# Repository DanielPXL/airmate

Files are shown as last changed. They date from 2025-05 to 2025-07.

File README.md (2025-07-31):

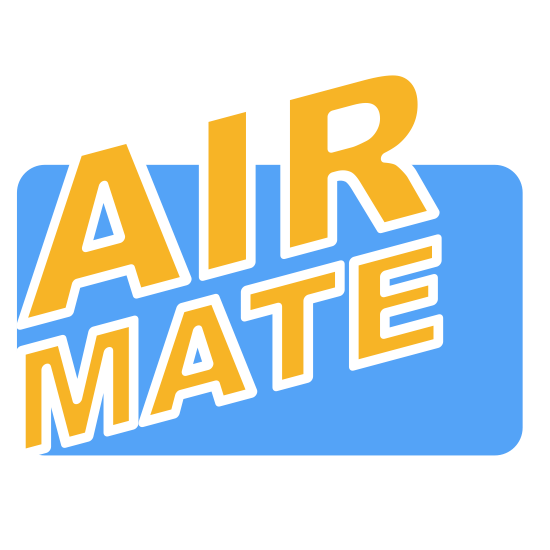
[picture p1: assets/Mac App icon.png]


---

Der _AirMate_ ist ein sich automatisch öffnendes Fenster, welches sich anhand von Sensordaten selbst öffnet. Er hostet außerdem eine Website, welche die Sensordaten anzeigt. Über diese und einen Knopf am Fenster selbst lässt sich das Fenster auch manuell öffnen.

Als Projekt ist es im Rahmen eines Moduls des Informatikstudiums entstanden. Es hatte dabei die Zielsetzung eines der Nachhaltigkeitsziele der UN zu erfüllen. Wir haben uns hier auf das Ziel der Inklusion konzentriert und haben ein Konzept erstellt welches Menschen mit Einschränkungen das alltägliche Leben leichter machen soll. Da wir mit dem CO2- und Temperatursensor schon geplant hatten war es für uns einfach diese noch zu erweitern um auch eine Einbruchssicherung zu erweitern.

# Software

Mittels einer API speisen wir die Wetterdaten aus dem Internet ein. Zusammen mit den Sensordaten, welche der ESP direkt erhält, entscheidet dieser dann ob das Fenster geöffnet werden sollte oder geschlossen und passt den jeweiligen Zustand an. Über den ESP selbst wird dann noch eine Website dargestellt welche die Sensordaten darstellt und es erlaubt das Fenster zu öffnen.

## Kompilieren

Voraussetzungen:

- Arduino IDE
- ESP32 Board in der Arduino IDE installiert
- Abhängigkeiten in der Arduino IDE installiert:
  - ArduinoJson von Benoit Blanchon
  - DHT Sensor Library von Adafruit
  - AccelStepper von Mike McCauley

Zum Kompilieren die Datei `AirMate.ino` in der Arduino IDE öffnen und auf den Upload-Button klicken. Der ESP sollte dann automatisch neu starten und die Website ist unter der IP-Adresse des ESP erreichbar.

## Webinterface

Das Webinterface wird auf dem ESP gehostet. Eine kompilierte Version des Webinterfaces ist bereits in diesem Repository enthalten. Wenn das Webinterface bearbeitet wurde, muss es neu kompiliert werden. Mehr dazu [hier](./src/AirMate/website/README.md).

# Hardware

## Sensoren

Diese könnten auch weggelassen werden und das Fenster nur über Knopf und Website geöffnet werden.

- DHT11
  Temperatur- & Feuchtigkeitssensor
- MH-Z19C
  CO2-Sensor
- KY-021
  Reedschalter / Magnetsensor

## ESP

Achtung Schaltplan sieht andere Pins vor als vorhanden.

- ESP32
- D1 Mini DC Powershield

## Motoren

Von der Leistung her sind sie auf ein Leichtholzfenster im Eigenbau ausgelegt

- Nema 17 mit A4988
  Stepper-Motor für das Öffnen des Fensters
- 28BYJ-48 mit ULN2003
  Stepper-Motor für das Betätigen das Verschlussmechanismus des Fensters

## 3D Druck

Modelle sind in den assets zu finden.

- Kasten und Deckel für Unterbringung des ESPS, sowie einiger Sensoren
- Anbringung für Motor
- Riegel für Verschluss
- Zahnrad für Öffnen
- Zahnschiene für Öffnen

# Beitragende

- [DanielPXL](https://github.com/DanielPXL)
- [Kaskary7](https://github.com/Kaskary7)
- [Oppermannt](https://github.com/Oppermannt)
- [TheSacredCactus](https://github.com/TheSacredCactus)
- [Tomerius135](https://github.com/Tomerius135)
- [Quantkas](https://github.com/Quantkas)

# Lizenz

Dieses Projekt ist unter der GPL3 lizenziert, siehe [LICENSE](./LICENSE).

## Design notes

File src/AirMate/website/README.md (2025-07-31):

# AirMate Webinterface

Innerhalb dieses Ordners befindet sich das Webinterface für den AirMate. Dieses ist in Vanilla JS, HTML und CSS geschrieben.

Das Webinterface wird in eine einzige HTML-Datei kompiliert, anschließend komprimiert und dann in einen C-Header umgewandelt, der in das AirMate-Projekt included wird. Dies ist **nicht** in dem Kompilierprozess des AirMate-Projekts enthalten und muss separat durchgeführt werden, wenn das Webinterface bearbeitet wurde.

Damit nicht jeder npm usw. installieren muss, um das AirMate-Projekt zu kompilieren, ist im Repository bereits eine kompilierte Version des Webinterface enthalten.

# Kompilieren

Folgendes muss installiert sein:

- Node.js und npm
- gzip
- xxd

Folgende Befehle zum Kompilieren ausführen:

```bash
npm install
npm run build
```

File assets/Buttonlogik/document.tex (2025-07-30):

\documentclass{article}
\usepackage[a4paper, top=2cm, bottom=2cm, left=2cm, right=2cm]{geometry}
\usepackage{tikz}
\usetikzlibrary{calc, positioning, shapes.misc, fit}

\pagestyle{empty}

\begin{document}
	\begin{center}
		\begin{tikzpicture}[
			round/.style={rounded corners=1.5mm, inner sep=4mm, draw, align=center, node distance=5cm},
			every node/.style={font=\normalsize},
			->, >=stealth,
			]
			
			% Hauptzustände
			\node[round, fill=orange!15] (Verriegeln) at (0,4) {Verriegeln};  
			\node[round, fill=orange!15, right=6cm of Verriegeln] (Entriegeln) {Entriegeln};
			\node[round, fill=red!15] (Verriegelt) at ($(Verriegeln)!0.5!(Entriegeln)+(0,6)$) {Verriegelt};
			\node[round, fill=gray!15] (GeschlossenL) at ($(Verriegeln)+(0,-6.5)$) {Geschlossen vor Verriegelung}; % Links unter Verriegeln
			\node[round, fill=gray!15] (GeschlossenR) at ($(Entriegeln)+(0,-6.5)$) {Geschlossen nach Entriegelung}; % Rechts unter Entriegeln
			\node[round, fill=blue!10] (Schließend) at ($(GeschlossenL)+(0,-6)$) {Schließend};
			\node[round, fill=blue!10] (Öffnend) at ($(GeschlossenR)+(0,-6)$) {Öffnend};
			\node[round, fill=green!20] (Offen) at ($(Schließend)!0.5!(Öffnend)$) {Offen};
			\node[round, fill=yellow!10] (StopSchließend) at ($(Schließend)+(0,-5)$) {Stop Schließen};
			\node[round, fill=yellow!10] (StopÖffnend) at ($(Öffnend)+(0,-5)$) {Stop Öffnen};
			\node[draw, dashed, rounded corners=2mm, inner sep=8mm, fit=(StopSchließend)(StopÖffnend), 
			label={[label distance=3mm]below:{Stop}}] {};
			\node[draw, dashed, rounded corners=2mm, inner sep=8mm, fit=(Entriegeln)(Verriegeln), 
			label={[label distance=3mm]above:{Schließmechanismus}}] {};
			\node[draw, dashed, rounded corners=2mm, inner sep=8mm, fit=(GeschlossenL)(GeschlossenR),
			label={[label distance=3mm]above:{Geschlossen}}] {};

			% Transitionen
			\path
			(Verriegelt) edge node[right] {button} (Entriegeln)
			(Entriegeln) edge node[right] {unlock\_done} (GeschlossenR)
			(GeschlossenR) edge node[left] {auto} (Öffnend)
			(GeschlossenL) edge node[right] {auto} (Verriegeln)
			(Verriegeln) edge node[left] {system\_lock} (Verriegelt)
			(Öffnend) edge node[above] {open\_done} (Offen)
			(Öffnend) edge node[right] {button} (StopÖffnend)
			(StopÖffnend) edge node[near end, left] {button} (Schließend)
			(Schließend) edge node[left] {close\_done} (GeschlossenL)
			(Schließend) edge node[left] {button} (StopSchließend)
			(StopSchließend) edge node[near end, right] {button} (Öffnend)
			(Offen) edge node[above] {button} (Schließend)
			;
			
		\end{tikzpicture}
	\end{center}
\end{document}

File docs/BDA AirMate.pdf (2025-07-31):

AirMate – Das automatische Fenster
Das Beste was Raumklima passiert ist seit der Erfindung von Zimmerpflanzen

Was ist der AirMate?
Der AirMate ist ein automatisches Fenster, das sich selbstständig ö7net oder schließt – basierend auf Sensordaten wie CO₂, Temperatur und Luftfeuchtigkeit. Zusätzlich bietet der AirMate eine Weboberfläche, über die man Sensordaten live einsehen und das Fenster manuell steuern kann – auch per Knopfdruck am Gerät selbst.
Das Projekt wurde im Rahmen eines Informatikmoduls entwickelt, und versteht sich in seiner derzeitigen Form als Prototyp.

Erste Schritte: Installation & Inbetriebnahme

### 1. Fenster einsetzen

Stellen Sie sicher, dass das AirMate-Fenster korrekt eingebaut und ist.
- Alle mechanischen Teile bewegen sich frei und sind nicht blockiert
- Etwaige freie Kabel wurden um den Rahmen herumgelegt

### 2. Airmate im Heim-WLAN anmelden

Voraussetzung: Arduino IDE mit ESP32 Support und Git installiert (siehe https://docs.espressif.com/projects/arduino-esp32/en/latest/installing.html)
1. AirMate Git-Repo clonen
2. src/AirMate/AirMate.ino ö7nen
3. WIFILogin.cpp ö7nen
4. WLAN-Daten in Zeile 5 und 6 ändern
5. Computer per USB mit dem AirMate verbinden
6. Projekt kompilieren und hochladen
7. USB-Kabel vom Computer entfernen
8. Stecker vom AirMate an eine Steckdose anschließen
9. USB-Kabel vom AirMate an ein USB-Netzteil anschließen
10. Motor an Steckdose anschließen

Bedienung
Die Benutzeroberfläche des Webinterfaces zeigt:
- Aktuelle Sensordaten (CO₂, Temperatur, Luftfeuchtigkeit)
- Aktuelle Wetterdaten
- Button zum manuellen ÖHnen/Schließen
- AirMate Logo für ö7nen von Einstellungen

Sensor- und Wetterdaten
Diese werden auf der Website direkt als Tabelle dargestellt, mit einem Klick auf diese ö7net sich eine ausführlicher Version mit allen Daten sowie dem aktuellen Status des Fensters.

Automatisch öHnen aktivieren und deaktivieren
Um das automatische Ö7nen des Fensters anhand vom aktuellen Raumklima zu aktivieren oder zu deaktivieren, klicken sie bitte einmal auf das AirMate-Logo in der rechten unteren Ecke, daraufhin ö7net sich die Einstellungen. Als obersten Punkt kann man dann auswählen ob sich das Fenster zur Zeit automatisch ö7nen soll oder nicht.

Achtung: Dieses Feature muss nachts nicht abgeschaltet werden, da in den Bedingungen für das ÖEnen des Fensters festgelegt ist, dass es sich nur am Tag automatisch öEnet. Bitte öEnen Sie das Fenster nachts manuell.

Einstellen der ÖHnungszeit
Um auszuwählen wie lange der AirMate das Fenster nach dem Ö7nen geö7net halten soll, klicken sie bitte einmal auf das AirMate-Logo in der rechten unteren Ecke, daraufhin ö7net sich die Einstellungen. Als untersten Punkt können sie dann auswählen, wie lange das Fenster mindestens geö7net sein soll bevor es sich wieder schließt.

Button zum manuellen ÖHnen und Schließen
Mittels eines Drucks auf en Button ist es jederzeit möglich das Fenster zu ö7nen oder zu schließen Dies funktioniert sowohl mit dem manuellen wie auch dem digitalen im Webinterface. Außerdem kann mit diesen der aktuelle Ö7nungs- oder Schließvorgang gestoppt werden.

Mit einem einfachen Druck auf den Button startet das Fenster bei geschlossenem Zustand den Vorgang des Ö7nens. Dafür wird zuerst die Verriegelung des Fensters geö7net, danach wird das Fenster geö7net. Erfolgt während dieses eine weitere Eingabe auf den Knopf, stoppt dieser Vorgang. Ein weiterer Druck auf den Button schließt das Fenster dann wieder, woraufhin dieses sich automatisch verriegelt.
Ist das Fenster geö7net, sorgt ein Druck auf den Button dafür, dass das Fenster sich anfängt zu schließen. Drückt man den Button ein weiteres Mal, während sich das Fenster schließt, stoppt dieser Vorgang. Ein weiterer Druck führt dazu, dass das Fenster sich wieder ganz ö7net.

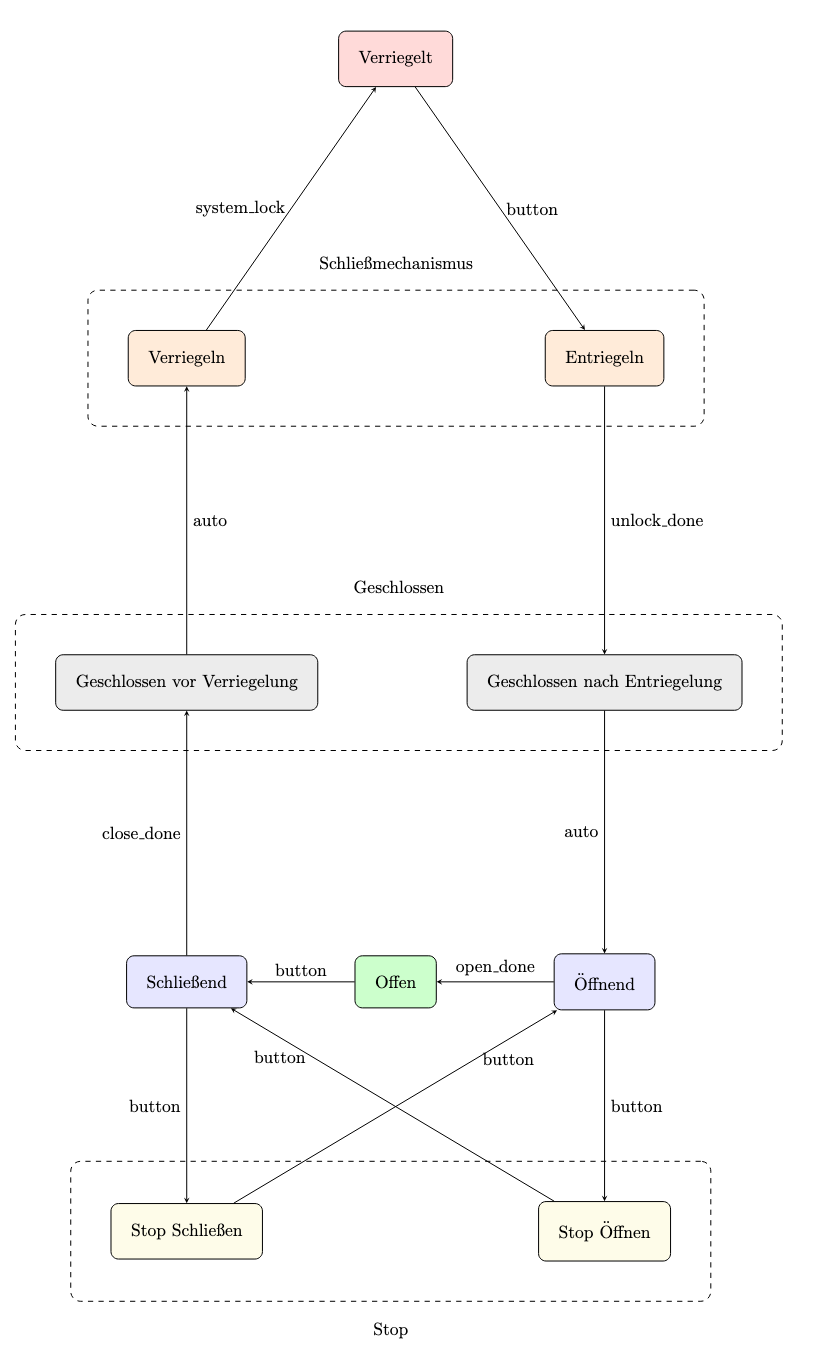
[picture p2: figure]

Sicherheit & Sensorik
Der AirMate verwendet folgende Sensoren:
- DHT11 – Temperatur & Luftfeuchtigkeit
- MH-Z19C – CO₂
- KY-021 – Magnetsensor zur Einbruchserkennung Auch bei Ausfall der Sensorik ist manuelle Steuerung möglich.

Aufgrund der Stärke der Motoren und der verbauten Zahnräder sind keine Verletzungen durch Quetschung zu befürchten. Bitte achten sie dennoch darauf, dass sich beim ÖEnen oder Schließen das Fensters sich nichts in dessen Bahn befindet.

No Copyright

The person who associated a work with this deed has dedicated the work to the public domain by waiving all of his or her rights to the work worldwide under copyright law, including all related and neighboring rights, to the extent allowed by law.

You can copy, modify, distribute and perform the work, even for commercial purposes, all without asking permission. See Other Information below.

Other Information

In no way are the patent or trademark rights of any person a?ected by CC0, nor are the rights that other persons may have in the work or in how the work is used, such as publicity or privacy rights. (https://creativecommons.org/publicdomain/zero/1.0/#ref-publicity-rights)

Unless expressly stated otherwise, the person who associated a work with this deed makes no warranties about the work, and disclaims liability for all uses of the work, to the fullest extent permitted by applicable law.

When using or citing the work, you should not imply endorsement by (https://creativecommons.org/publicdomain/zero/1.0/#ref-endorsement) the author or the a?irmer.

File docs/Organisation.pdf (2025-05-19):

Kalenderwochen:
KW 21 | KW 22 | KW 23 | KW 24 | KW 25 | KW 26 | KW 27
Aufgaben: | Erstellung Fenster-Holzmodell mit Plexiglasscheibe
3D Druck Zahnrad + Verschießsystem ( + halterungen am Fenster etc.)

Modelierung und Druckung des Gehäuses für Sensoren, Aktoren, Stromversorgung & ESP

Schaltplanerstellung aller Sensoren und Aktoren + Löten Programmierung und Test von Sensoren und Aktoren Programmierung des Webinterfaces
Pr. & Tes. des Magnetsensors
Gesammttestung des Airmates

Nameslegende:
Tom W. Daniel | Tizian | Lukas H. Tom O. | Lukas K.

# AirMate Ablaufplan Übersicht

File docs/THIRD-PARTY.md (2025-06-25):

## MH-Z-CO2-Sensors

Copyright (c) 2018 Tobias Schürg

Permission is hereby granted, free of charge, to any person obtaining a copy
of this software and associated documentation files (the "Software"), to deal
in the Software without restriction, including without limitation the rights
to use, copy, modify, merge, publish, distribute, sublicense, and/or sell
copies of the Software, and to permit persons to whom the Software is
furnished to do so, subject to the following conditions:

The above copyright notice and this permission notice shall be included in all
copies or substantial portions of the Software.

THE SOFTWARE IS PROVIDED "AS IS", WITHOUT WARRANTY OF ANY KIND, EXPRESS OR
IMPLIED, INCLUDING BUT NOT LIMITED TO THE WARRANTIES OF MERCHANTABILITY,
FITNESS FOR A PARTICULAR PURPOSE AND NONINFRINGEMENT. IN NO EVENT SHALL THE
AUTHORS OR COPYRIGHT HOLDERS BE LIABLE FOR ANY CLAIM, DAMAGES OR OTHER
LIABILITY, WHETHER IN AN ACTION OF CONTRACT, TORT OR OTHERWISE, ARISING FROM,
OUT OF OR IN CONNECTION WITH THE SOFTWARE OR THE USE OR OTHER DEALINGS IN THE
SOFTWARE.

## DHT-sensor-library

Copyright (c) 2020 Adafruit Industries

Permission is hereby granted, free of charge, to any person obtaining a copy
of this software and associated documentation files (the "Software"), to deal
in the Software without restriction, including without limitation the rights
to use, copy, modify, merge, publish, distribute, sublicense, and/or sell
copies of the Software, and to permit persons to whom the Software is
furnished to do so, subject to the following conditions:

The above copyright notice and this permission notice shall be included in all
copies or substantial portions of the Software.

THE SOFTWARE IS PROVIDED "AS IS", WITHOUT WARRANTY OF ANY KIND,
EXPRESS OR IMPLIED, INCLUDING BUT NOT LIMITED TO THE WARRANTIES OF
MERCHANTABILITY, FITNESS FOR A PARTICULAR PURPOSE AND NONINFRINGEMENT.
IN NO EVENT SHALL THE AUTHORS OR COPYRIGHT HOLDERS BE LIABLE FOR ANY CLAIM,
DAMAGES OR OTHER LIABILITY, WHETHER IN AN ACTION OF CONTRACT, TORT OR
OTHERWISE, ARISING FROM, OUT OF OR IN CONNECTION WITH THE SOFTWARE OR THE USE
OR OTHER DEALINGS IN THE SOFTWARE.

## ArduinoJson

Copyright © 2014-2025, Benoit BLANCHON

Permission is hereby granted, free of charge, to any person obtaining a copy of this software and associated documentation files (the “Software”), to deal in the Software without restriction, including without limitation the rights to use, copy, modify, merge, publish, distribute, sublicense, and/or sell copies of the Software, and to permit persons to whom the Software is furnished to do so, subject to the following conditions:

The above copyright notice and this permission notice shall be included in all copies or substantial portions of the Software.

THE SOFTWARE IS PROVIDED “AS IS”, WITHOUT WARRANTY OF ANY KIND, EXPRESS OR IMPLIED, INCLUDING BUT NOT LIMITED TO THE WARRANTIES OF MERCHANTABILITY, FITNESS FOR A PARTICULAR PURPOSE AND NONINFRINGEMENT. IN NO EVENT SHALL THE AUTHORS OR COPYRIGHT HOLDERS BE LIABLE FOR ANY CLAIM, DAMAGES OR OTHER LIABILITY, WHETHER IN AN ACTION OF CONTRACT, TORT OR OTHERWISE, ARISING FROM, OUT OF OR IN CONNECTION WITH THE SOFTWARE OR THE USE OR OTHER DEALINGS IN THE SOFTWARE.

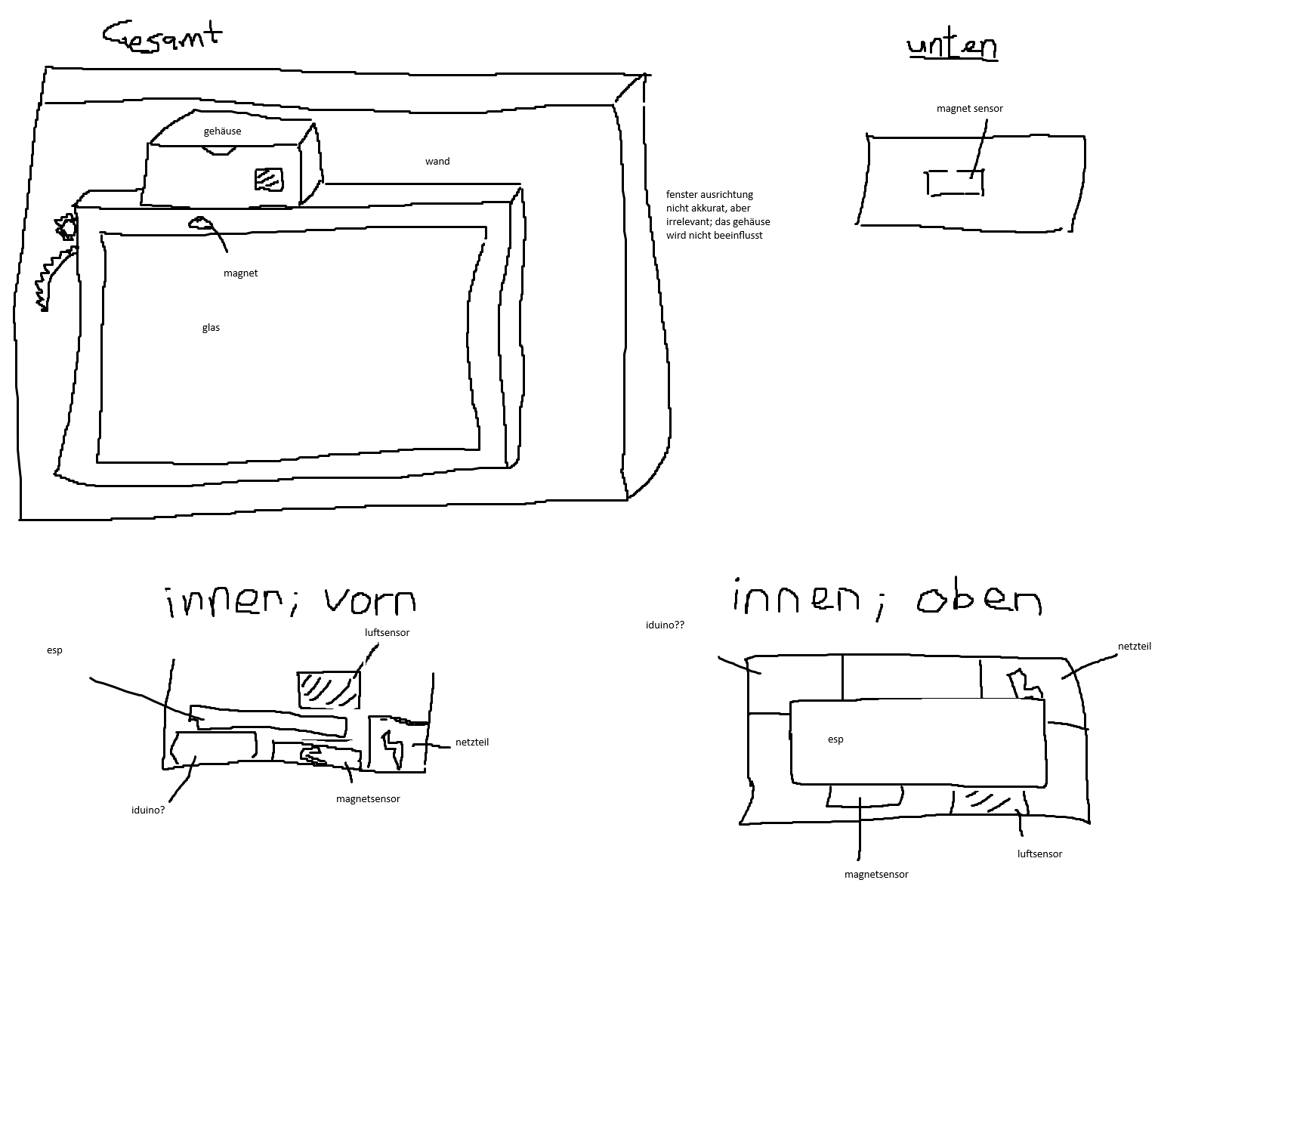
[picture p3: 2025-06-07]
assets/Gehäuse Plan.png

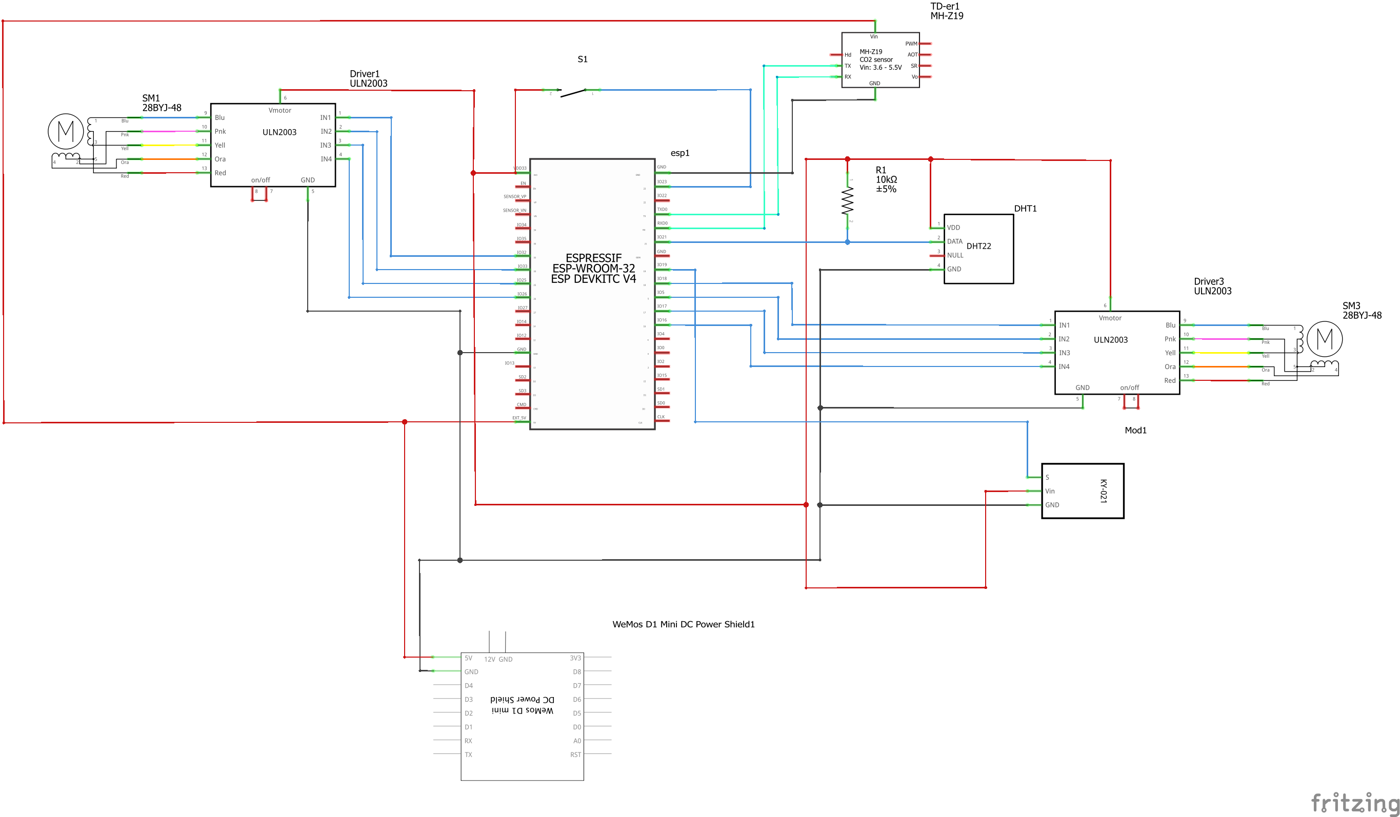
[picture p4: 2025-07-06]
assets/Schaltung/SchaltplanFenster_Schaltplan.png

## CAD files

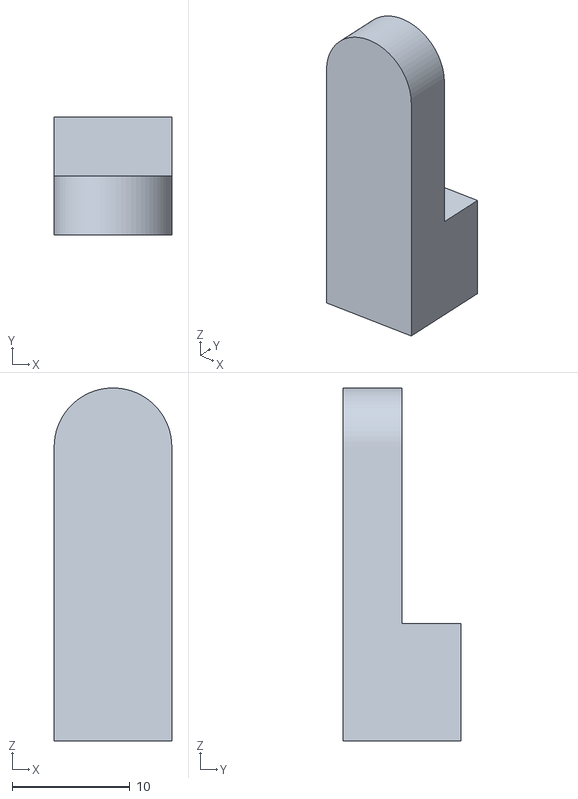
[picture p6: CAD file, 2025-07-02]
assets/3DModels/Verschlussteil v5.stl
10.0 x 10.0 x 30.0

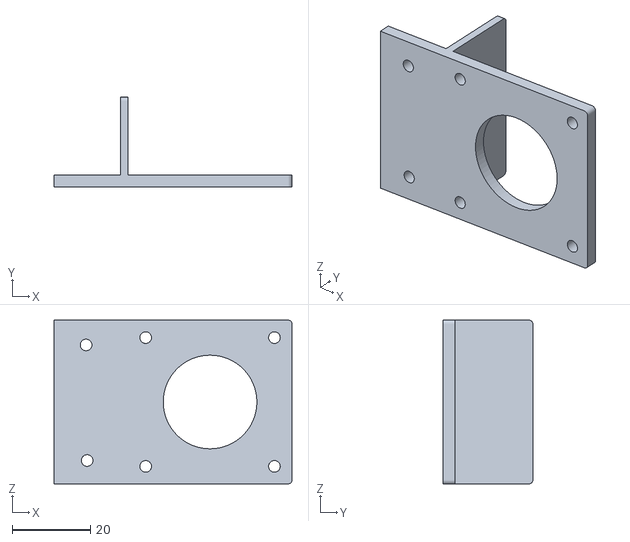
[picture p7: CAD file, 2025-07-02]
assets/3DModels/Ramblecaster v2.stl
61.0 x 23.0 x 42.0

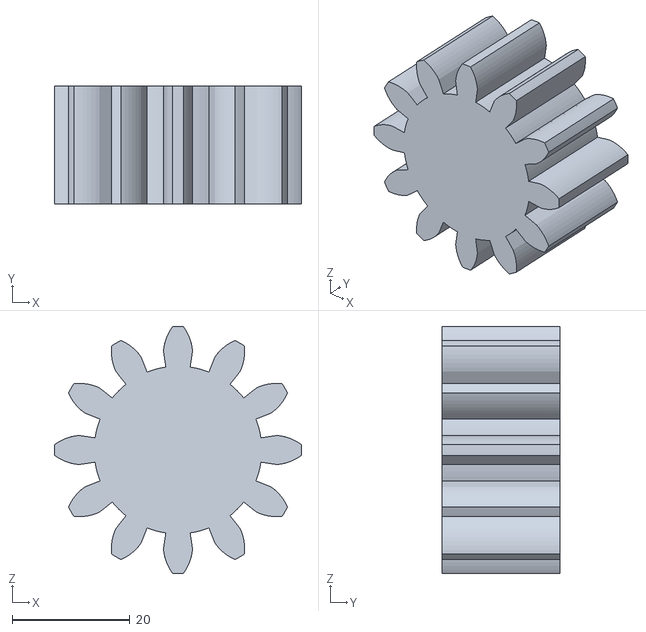
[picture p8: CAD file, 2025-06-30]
assets/3DModels/Zahnrad v2.stl
42.0 x 20.0 x 42.0

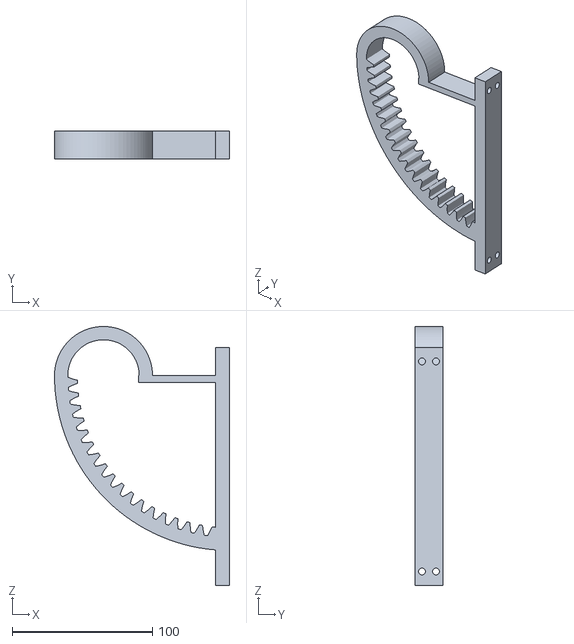
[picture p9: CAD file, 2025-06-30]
assets/3DModels/Zahnrad Befestigung v3.stl
125.0 x 20.0 x 185.0

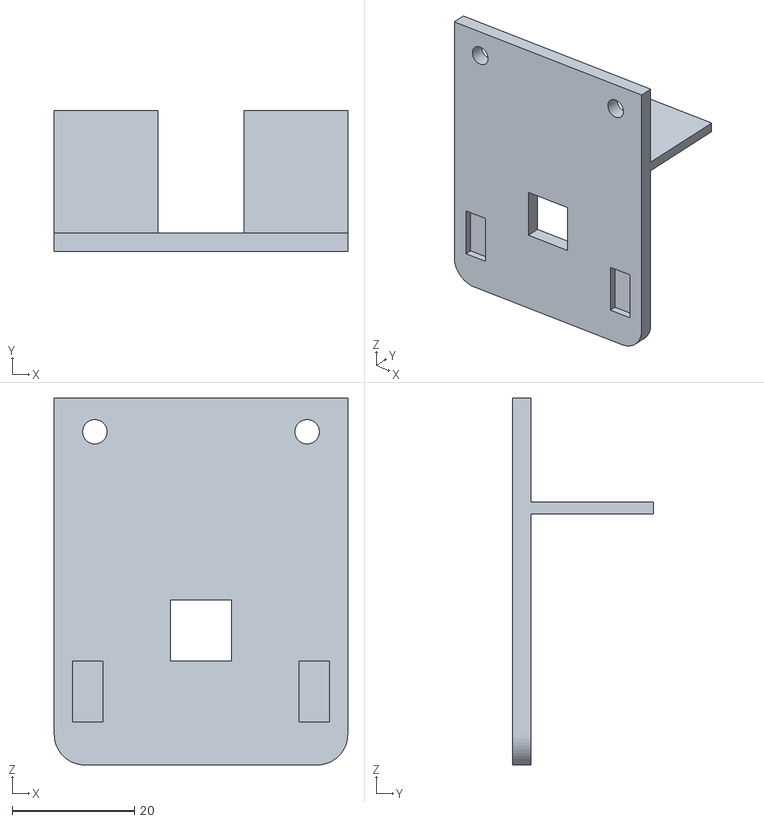
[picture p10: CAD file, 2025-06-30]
assets/3DModels/Mumblecaster fr v3.stl
48.0 x 23.0 x 60.0

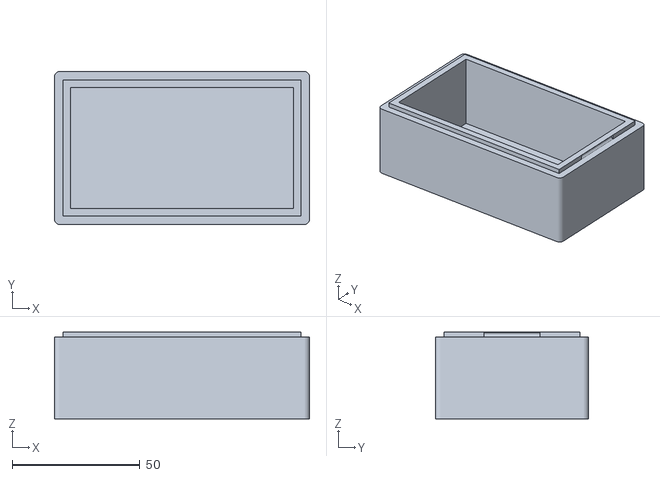
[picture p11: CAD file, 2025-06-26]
assets/3DModels/Deckel v7.stl
100.0 x 60.0 x 34.0

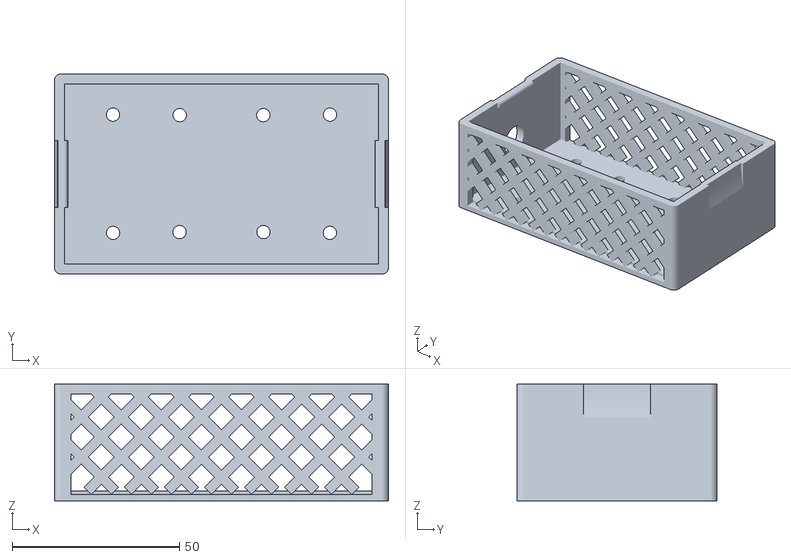
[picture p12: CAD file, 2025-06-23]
assets/3DModels/Gehäuse v6.stl
100.0 x 60.0 x 35.0

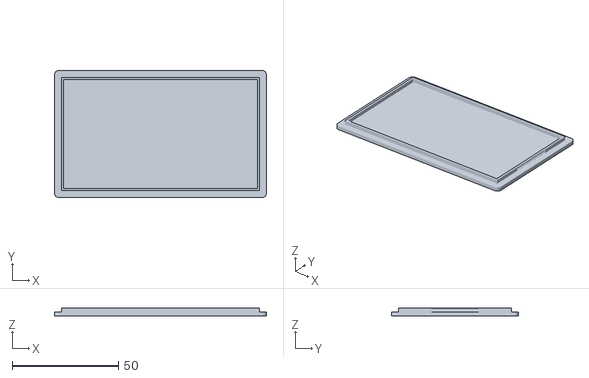
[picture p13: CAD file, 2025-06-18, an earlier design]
assets/3DModels/Deckel v6.stl
100.0 x 60.0 x 4.00

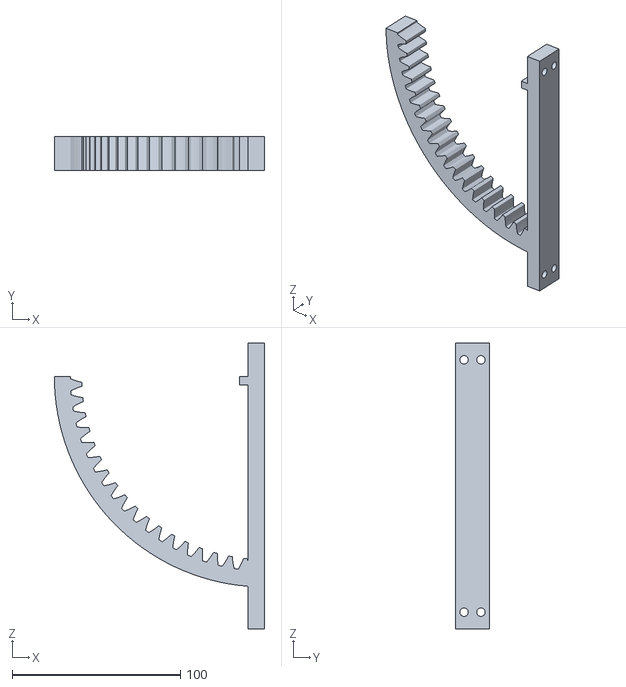
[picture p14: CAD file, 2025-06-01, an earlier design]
assets/3DModels/Zahnrad Befestigung v2.stl
125.0 x 20.0 x 170.0

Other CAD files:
assets/3DModels/Verschlussteil v0.stl

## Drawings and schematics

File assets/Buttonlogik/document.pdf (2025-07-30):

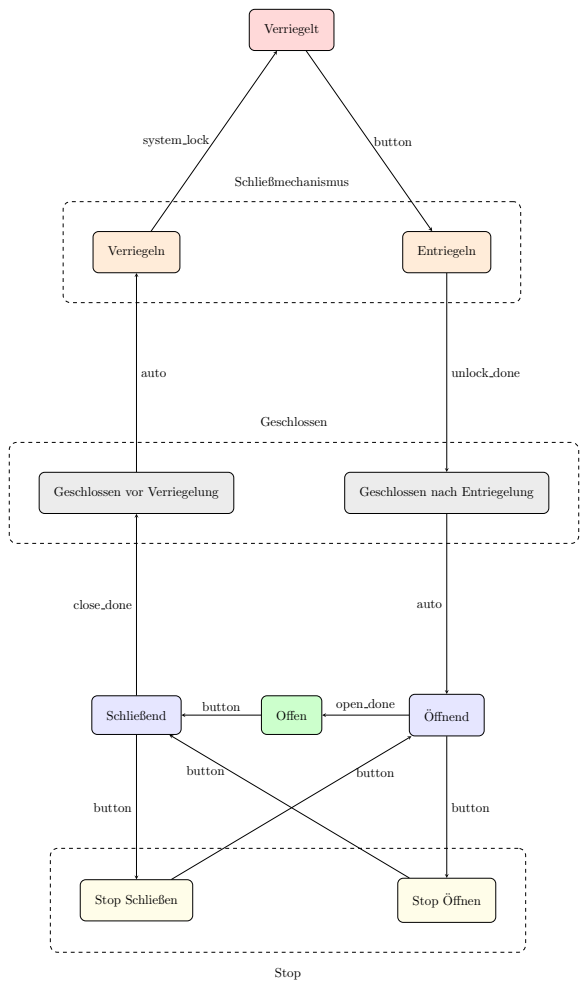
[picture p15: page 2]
Verriegeln; Entriegeln; Verriegelt; Geschlossen vor Verriegelung; Geschlossen nach Entriegelung; Schließend; Offen; Offnend ¨; Stop Schließen; Stop Offnen ¨; Stop; Schließmechanismus; Geschlossen; button; unlock done; auto; system lock; open done; close done

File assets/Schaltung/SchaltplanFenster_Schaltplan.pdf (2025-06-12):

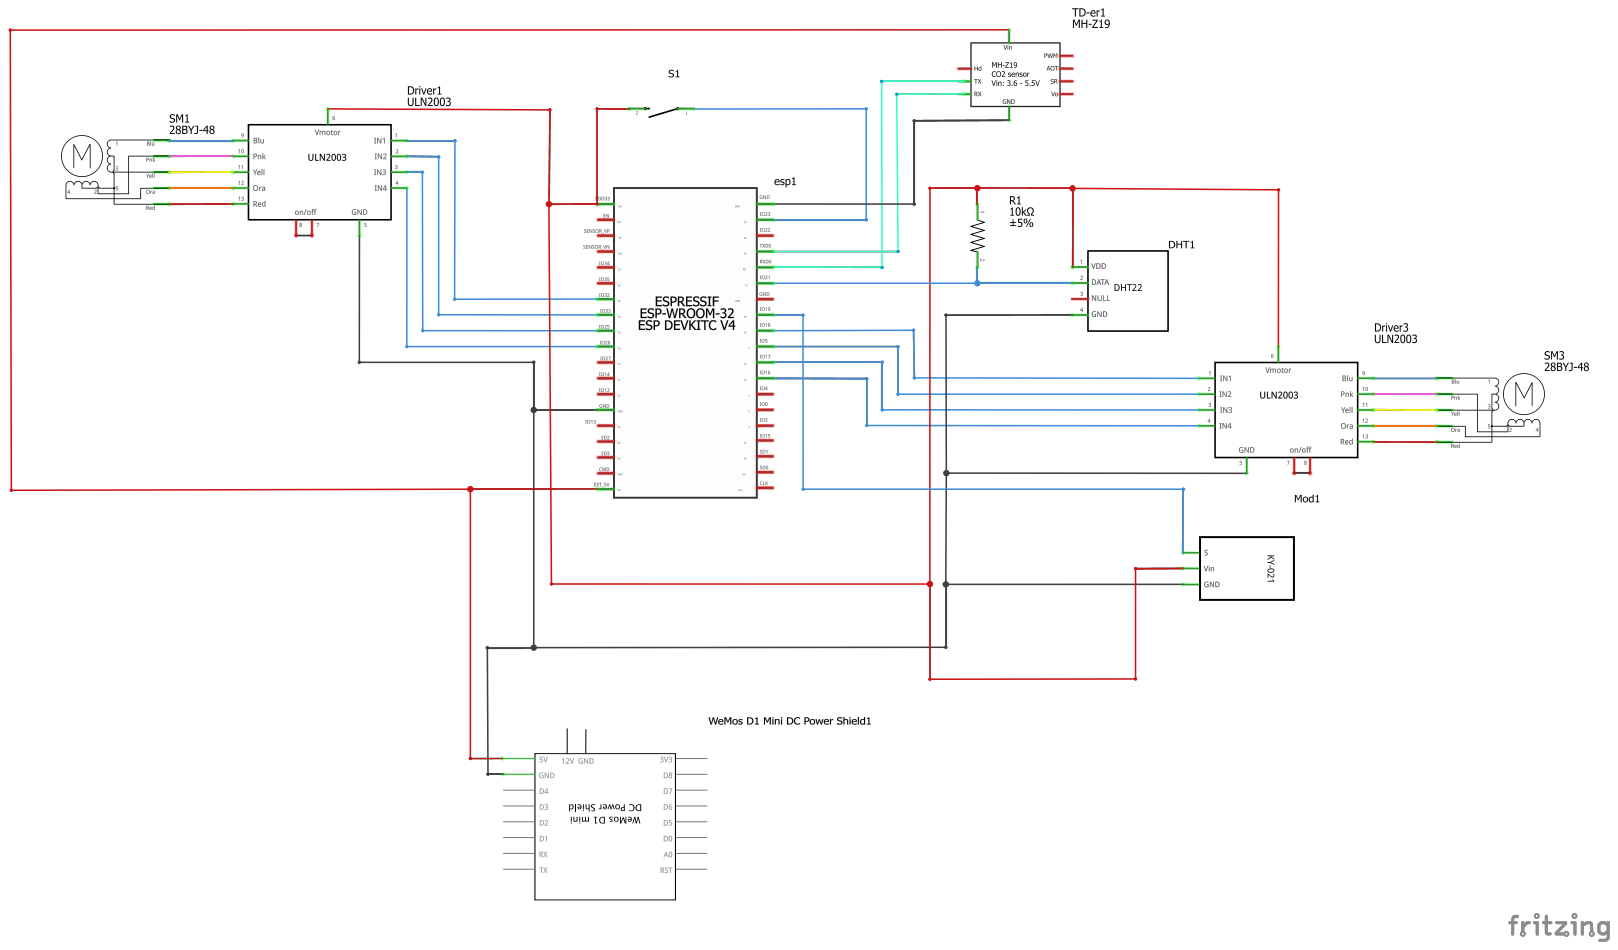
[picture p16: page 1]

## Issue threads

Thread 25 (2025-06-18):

Aufgabe 1: Präsentation eures Projekts im Blog

Quantkas, 2025-06-18:
Präsentiert auf eurem Gruppenblog euch und euer Projekt anschaulich.
Nutzt dazu die Punkte aus der mündlichen Präsentation. Nutzt verschiedene Präsentationsformen (Skizzen, Fotos, Screenshots, Text, Video, …). **Es muss mindestens ein Video enthalten sein, dass das funktionierende Projekt zeigt!** Ihr dürft gerne wieder kreativ werden (z.B. Elevator Pitch, „echter“ Einsatz des Systems, … ). Die Funktionsweise könnt ihr hier auf die Sicht der Nutzenden beschränken (da die technische Sicht Teil der Dokumentation ist!). Beschreibt den Prozess der Entstehung und reflektiert euer finales Projekt. Beschreibt, inwiefern euer Projekt das Nachhaltigkeitsziel (oder die Ziele) erreichen kann. Betrachtet euer Projekt auch kritisch und geht dabei beispielsweise auf Fragen ein, wie: Wem nützt es tatsächlich? Welche nicht bedachten Nachteile oder Gefahren birgt die Nutzung / der Einsatz eures Produkts? Welche gesellschaftlichen Auswirkungen könnte eine Markteinführung eures Produkts haben? …

**Beachtet weiterhin allgemeine Vorgaben an Blogs (siehe persönlicher Blog)!**

Closed 2025-08-01.

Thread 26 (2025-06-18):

Aufgabe 2: Beschreibung und Reflexion der Zusammenarbeit

Quantkas, 2025-06-18:
Wir hatten in der Vorlesung verschiedene Aspekte zu Gruppenarbeit besprochen. Wie lief eure Gruppenarbeit ab? Beschreibt eure
Zusammenarbeit sowie ggf. die Aufteilung von Arbeiten (ohne Nennung von Namen). Geht dabei u.a. auf die folgenden Aspekte ein:
- Welche Tools und Methoden habt ihr zur Zusammenarbeit und Kommunikation genutzt?
- Welche Tools und Methoden haben sich als besonders hilfreich erwiesen und warum?
- Welche Tools und/oder Methoden habt ihr ggf. verworfen und warum?
- Wie bewertet ihr euren Zeitplan?
- Was waren Stolpersteine in der Gruppenarbeit und wie konntet ihr sie beseitigen?
- …

---
Nutzung folgender Vorlesungsfolien:
- Vorlesung 11 - Teil 1: Kommunikation
- Vorlesung 11 - Teil 2: Konflikte
- Vorlesung 03 - Teil1: Zeitmanagement
- Vorlesung 05: Kreativität

Closed 2025-08-01.

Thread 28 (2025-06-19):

Programmierung der Automatisierung

Kaskary7, 2025-06-19:
Wann wird geöffnet, bzw wie häufig werden die Sensoren ausgelesen.
Wann wird geschlossen.(Timer usw.)

Quantkas, 2025-06-19:
Und wenn offen per Sensordaten, dann 5-7min, würde ich sagen

DanielPXL, 2025-06-19:
> Wann wird geöffnet, bzw wie häufig werden die Sensoren ausgelesen. Wann wird geschlossen.(Timer usw.)

Die Sensoren werden jetzt gerade alle 10s (siehe Airmate.ino) ausgelesen, demnach wird auch alle 10s entschieden, ob sich das Fenster öffnen soll. Die Sensorwerte werden auch nach dem Öffnen weiterhin alle 10s aktualisiert, aber das Fensteröffnen wird nur entschieden, wenn das Fenster gerade geschlossen ist (Die Sensoren werden immernoch aktualisiert, damit die Werte dann auf der Website angezeigt werden können). Das ist auch schon implementiert.

Das Bestimmen, ob geschlossen werden soll, ist jetzt noch nicht geschrieben, wird aber wohl in Window.ino passieren, in dem großen switch-Block. Da würd ich vorschlagen, dass wir 5min warten und dann gucken, ob die Werte besser geworden sind. Wenn ja, dann schließen, wenn nein, dann so weitermachen (also ohne nochmal 5min zu warten, sondern dann stets die Werte evaluieren).

Quantkas, 2025-06-19:
> ist aber meiner Meinung nach viel zu übertrieben

Stimmt. Können ja das im Hinterkopf behalten und noch machen, wenn wir genug Zeit haben. Ansonsten, in dem Issue Anforderungen Wordpress müssen wir auch Verbesserungen und Erweiterungsideen hinzufügen.
Bin die Vorlesungen nochmal durchgegangen...

Closed 2025-07-05.

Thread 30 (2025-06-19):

Projektdokumentation WordPress

Quantkas, 2025-06-19:
**Verpflichtende Inhalte der Dokumentation**
- [x] Motivation oder Problemstellung: Welches Problem löst eurer Projekt?
- [x] Anforderungskatalog: detaillierte Funktionsbeschreibung
- [x] Ausführlicher Projektplan und Einteilung von Aufgaben und Verantwortlichkeiten.
- [x] Risikomanagement beschreiben
- [x] Beschreibung der 3D-Modellierung / Laser-Cut
- [x] Beschreibung der Hardware-Entwicklung
- [x] Beschreibung der Software-Entwicklung
- [x] Beschreibung der Systemarchitektur und Schnittstellen
- [x] Eine Demonstration der Funktionen (mit Video)
- [x] Fazit, Lessons Learned und mögliche Verbesserungen und Erweiterungsideen
- [x] Parallel zur Projektdokumentation: Projektfortschritt in einem Entwicklungsblog dokumentieren (**mindestens 8 Einträge**)

---
Teilweise werden die Punkte durch die Aufgabenblätter behandelt.

Quantkas, 2025-06-27:
Habe schonmal soweit alle weiteren nötigen Seiten in Wordpress erstellt (und halt leer, nur mit Überschrift veröffentlicht). Habe hoffentlich an alles gedacht und ist so für euch ok und verständlich, wie ich es gemacht habe.

Closed 2025-08-01.

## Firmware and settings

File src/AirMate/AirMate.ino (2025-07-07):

#include "Window.h"
#include "Weather.h"
#include "WIFILogin.h"
#include "WebInterface.h"
#include "Sensors.h"
#include "Log.h"

void setup() {
#if LOGGING_ENABLED
  Serial.begin(9600);
#endif
  wifi_connect();
  webinterface_setup();
  window_setup();
  sensors_setup();

  // Bei startup einmal schon updaten, sonst wird erst 30s gewartet
  weather_update();
  sensors_update();
}

void loop() {
  // Wetterdaten alle 60s updaten
  // Sensordaten alle 10s updaten
  static uint64_t lastWeatherUpdate = 0;
  static uint64_t lastSensorUpdate = 0;
  uint64_t now = millis();
  if (now - lastWeatherUpdate > 60000) {
    lastWeatherUpdate = now;
    weather_update();
  }

  if (now - lastSensorUpdate > 10000) {
    lastSensorUpdate = now;
    sensors_update();
  }

  window_loop();
  webinterface_loop();
  sensors_loop();
}

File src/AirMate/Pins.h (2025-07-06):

#ifndef PINS_H
#define PINS_H

#define BUTTON_PIN 21
#define REEDSENSOR_PIN 23
#define DTH11_PIN 22
#define MH_Z19_TX 17
#define MH_Z19_RX 16

#define LOCKMOTOR_PINS 14, 15, 26, 25
#define GEARMOTOR_PINS 5, 33

#endif

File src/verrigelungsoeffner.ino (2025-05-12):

#include <Stepper.h>

// Anzahl der Schritte pro Umdrehung
#define STEPS 1024

// Motorgeschwindigkeit in RPM
#define MOTOR_RPM 10

const int onButtonPin = 4;

int on = 1;

boolean open = false;

Stepper stepper(STEPS, 8, 10, 9, 11); // Motor Pins

void setup()
{
  pinMode(onButtonPin, INPUT_PULLUP);

  Serial.begin(9600);
}

void loop()
{
    on = digitalRead(onButtonPin);
    Serial.println(on);
    Serial.println(open);
    if (on == LOW && open){

      stepper.setSpeed(MOTOR_RPM);
      stepper.step(-STEPS);
      
      Serial.println("on is pushed!");
      delay(1000);
      open = false;

    }else if ( on == LOW && !open){

      stepper.setSpeed(MOTOR_RPM);
      stepper.step(STEPS);
      
      Serial.println("off is pushed!");
      delay(1000);
      open = true;

    }
  
}

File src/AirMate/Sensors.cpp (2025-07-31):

#include "esp32-hal-gpio.h"
#include <stdint.h>
#include <DHT.h> // DHT sensor library von Adafruit
// -------------------------------import für WifWaf Implementierung---
#include <HardwareSerial.h>
#include  "MHZ19.h" //MH-Z 19 CO2 Sensor library von WifWaf
//--------------------------------------------------------------------

#include "Pins.h"
#include "Weather.h"
#include "Sensors.h"
#include "Window.h"
#include "Log.h"

#define DHTTYPE DHT11

#define SCHALTminDewPoint 5.0 // minimaler Taupunktunterschied, bei dem das Fenster öffnen soll

bool g_autoEnabled = false;

//Messwerte
float g_temperature = 20;
float g_humidity = 55;
int32_t g_co2ppm = 1200;
float g_dewPoint = 20;

//Schwellwerte 
const float HUMIDITY_THRESHOLD = 60;
const float CO2THRESHOLD = 1000;
const float OPTIMAL_TEMP = 22;
const float MAX_WINDSPEED = 35;

DHT dht(DTH11_PIN, DHTTYPE);
MHZ co2(MH_Z19_RX, MH_Z19_TX, MHZ19C);

//----------------------------------------Co2 mit WifWaf Library -----------------------------
HardwareSerial mhzSerial(2); // Erstelle eine Instanz von HardwareSerial für UART2
MHZ19 mhz19; // Erstelle ein Objekt der MHZ19-Klasse
//--------------------------------------------------------------------------------------------


void sensors_setup() {
  // button setup
  pinMode(BUTTON_PIN, INPUT_PULLDOWN);

  // Reed sensor setup
  pinMode(REEDSENSOR_PIN, INPUT);

  // dht sensor setup
  dht.begin();

  //--------------------------------------------Setup CO2-----------------------------
  mhzSerial.begin(9600, SERIAL_8N1, MH_Z19_RX, MH_Z19_TX); // Serielle Kommunikation mit dem MH-Z19 starten
  mhz19.begin(mhzSerial); // MH-Z19-Bibliothek mit der seriellen Schnittstelle verbinden

  // Optional: Sensor kalibrieren (nur einmalig, wenn nötig!)
  mhz19.calibrate(); // Automatische Basiskalibrierung (ABC) einschalten
  // mhz19.calibrateZero(); // Kalibrierung auf 400ppm (nur wenn der Sensor in frischer Luft ist!)

  //---------------------------------------------------------------------------------
}

// Wird nur alle 10s ausgeführt
void sensors_update() {
  // DHT11 lesen und g_temperature und g_humidity updaten
  float temp = dht.readTemperature();
  float hum = dht.readHumidity();

  if (!isnan(temp) && !isnan(hum)) {
    g_temperature = temp;
    g_humidity = hum;

    // Taupunkt hängt von Temperatur und Luftfeuchtigkeit ab,
    // also auch updaten
    g_dewPoint = sensors_taupunkt(g_temperature, g_humidity);
  }

  // CO2-Sensorwert updaten
  g_co2ppm = mhz19.getCO2();

  // Falls shouldOpen(), öffnen
  if (sensors_shouldOpen()) {
    window_startOpening();
  }
}

bool sensors_shouldOpen() {
  if (!g_autoEnabled) {
    return false;
  }

  // Öffnungsparameter
  // Nachts nicht lüften
  if (!g_weatherIsDay) {
    return false;
  }

  // Wenns zu windig ist nicht lüften
  if (g_weatherWindSpeed > MAX_WINDSPEED) {
    return false;
  }

  // Wenn Niederschlag nicht lüften
  if (g_weatherPrecipitation > 0) {
    return false;
  }

  // C02 auf unter 1200ppm halten
  if (g_co2ppm >= 1200) {
    return true;
  }

  // Taupunkt
  float deltaTP = g_dewPoint - g_weatherDewPoint;
  if (deltaTP > SCHALTminDewPoint) {
    return true;
  }

  // Temperatur auf 22°C regeln
  if (g_temperature >= OPTIMAL_TEMP && g_weatherTemperature <= OPTIMAL_TEMP) {
    return true;
  }

  return false;
}

float sensors_taupunkt(float t, float r) {
  float a, b;

  if (t >= 0) {
    a = 7.5;
    b = 237.3;
  } else if (t < 0) {
    a = 7.6;
    b = 240.7;
  }

  // Sättigungsdampfdruck in hPa
  float sdd = 6.1078 * pow(10, (a*t)/(b+t));

  // Dampfdruck in hPa
  float dd = sdd * (r/100);

  // v-Parameter
  float v = log10(dd/6.1078);

  // Taupunkttemperatur (°C)
  float tt = (b*v) / (a-v);
  return tt;
}

// Wird so oft wie möglich ausgeführt
void sensors_loop() {
  // Button prüfen
  // Solange Button gedrückt wird, wird kein weiterer Toggle ausgelöst
  static bool buttonOldPush = false;
  bool buttonPush = digitalRead(BUTTON_PIN) == HIGH;
  if (buttonPush && !buttonOldPush) {
    // Button wurde gedrückt
    window_toggleOpen();
  }

  // Buttonstatus speichern
  buttonOldPush = buttonPush;

  if (g_state == State::Closed && digitalRead(REEDSENSOR_PIN) == LOW) {
    // Das Fenster sitzt nicht am Rahmen sollte aber zu sein
    g_state == State::Alarm;
  }
}

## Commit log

2025-05-08 Update README.md
    Erster Vorschlag für einen README Text. Spätere Funktionen und Anleitungen folgen.
2025-05-08 Update README.md
    Alten Text verworfen und neu verfasst
2025-05-19 AirMate Code Datei + Orderner Erstellt
    Änderung vom Variablennamen Stepper zu LockStepper für späteres unterscheiden der beiden Stepper
2025-05-19 Erstellung Projektablaufplan Excel
    Bearbeitung im team am 19.05. 14:30 Final.
    [Projektablaufplan.xlsx]
2025-06-09 Anfänge des Schaltplans
    [SchaltplanFenster.fzz]
2025-06-11 Schaltplan fertig
    [SchaltplanFenster.fzz]
2025-06-11 Jetzt aber fertig die Schaltung
    [SchaltplanFenster.fzz]
2025-06-12 PDF Schaltplan
    [SchaltplanFenster.fzz]
2025-06-18 Update Sensor.Ino
    Einlesen des DHT,s sowie berechnung des Taupunktes und demenstprechende Aufrufung des Fensteröffnens.
2025-06-18 Ergänzende Kommentare und Struckturierungen
2025-06-18 buttonPressed zu Lokal Geändert
2025-06-18 Änderung der Variablen zu float
2025-06-18 Gehäuse 3D Modell
    [Gehäuse v6.stl]
2025-06-18 Löcher für Button und Schrauben hinzugefügt + Deckel
    [Deckel v6.stl, Gehäuse v6.stl]
2025-06-19 Buttonlogik überarbeitet. Manuell kann man jetzt Stoppen bei gewünschter Fensteröffnung.
2025-06-19 Hilfsmethoden Ansteuerung Motor.
2025-06-20 Buttonlogik gefixt und window_loop entfernt, da gedoppelt war mit window_buttonToggle
2025-06-23 Änfange der Website
2025-06-23 Gehäuse Update - Gitter verstärkt
    [Gehäuse v6.stl]
2025-06-25 Website fast fertig, nur der Knopf ist noch nicht fertig implementiert
2025-06-26 Deckel etwas "verlängert" damit alles reinpasst
    [Deckel v7.stl]
2025-06-26 .ino Dateien durch .cpp und .h Dateien ersetzt. Hoffentlich funktionierts
2025-06-27 Co2-Sensor auslesen.
2025-06-30 Aufräumen, Logging abstrahieren, Motor-Grundgerüst erweitert
2025-06-30 Add files via upload
    Aktuelle Versionen der STL Dateien
    [Zahnrad Befestigung v3.stl, Zahnrad v2.stl]
2025-06-30 Update zu Accelstepper
    Implementierung von öffnen und schließen des Fensters, Konstanten müssen an die Realen gegebenheiten noch angepasst werden
2025-06-30 Button Fix and Fix motorsyntax
    [Sensors.cpp, Window.cpp]
2025-07-01 Implementierung mittels WifWaf Library und Hardware Serial
    Bisher noch auskomentiert
2025-07-01 Verschoenert und aufgeraeumt
2025-07-01 Darkmode Farben angepasst mit sanftem Uebergang und nun unnötige Klassen entfernt
2025-07-02 Das was wir brauchen unkommentieren
2025-07-02 Rechtschreibfehler fixen, Wetterdaten in header schreiben
    [Sensors.cpp]
2025-07-02 Main und footer background farbe gewechselt
2025-07-02 Fenster offen timer
2025-07-02 Motor, website timer
2025-07-03 Motorsteps anpassen
2025-07-03 Lüftenpopup und Wetterdatenpopup
2025-07-03 Buttonlogik und gear und lock Stepper
2025-07-03 Website paused state fix, button in eigenen loop bewegt, Motoren angepasst
    [AirMate.ino, Sensors.cpp, Window.cpp]
2025-07-04 Open timer von website auf esp übertragen
2025-07-06 Pins anpassen, Motor anpassen, Reedsensor schneller als alle 10s ausführen
2025-07-30 StateChart Buttonlogik
2025-07-30 Buttonlogik StateChart
2025-07-30 Korriegierter StateChart der Buttonlogik.
2025-07-31 Buttonlogik LaTeX temporäre Dateien entfernen
